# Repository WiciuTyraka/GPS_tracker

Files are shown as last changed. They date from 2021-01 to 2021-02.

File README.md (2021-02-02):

# Rocket Localization System

## About

[PUT Rocket Lab](https://tyraka.pl/) jest Kołem Naukowym z Politechniki Poznańskiej zajmującym się projektowaniem, budowaniem oraz testowaniem technologii
rakietowych. Flagowym projektem zespołu jest budowa rakiety sondażowej
Hexa 2 napędzanej hybrydowym silnikiem rakietowym. Jednym z większych problemów, z jakimi przychodzi zmagać się inżynierom budującym
rakiety, jest ich odzysk. Podczas testów rakieta zostaje wystrzelona w
przestrzeń. Wysokość oraz uzyskiwana prędkość obiektu jest oszacowana z
dużą dokładnością. Komplikacje pojawiają się przy estymowaniu miejsca
spadku rakiety, gdyż jest ono zależne w głównej mierze od powodzenia się
wszystkich procedur lądowania oraz w dużym stopniu od czynników meteorologicznych. Istotą odzysku jest zlokalizowanie rakiety w celu znalezienia
części, które są zdatne do ponownego użycia oraz tych, które już nie zadziałają, ale by zanieczyszczały środowisko. Większość zespołów decyduje
się na bardzo drogie komercyjne rozwiązania, które mimo wszystko nie są
wolne od ograniczeń. W tym repozytorium przedstawiony jest autorski projekt systemu lokalizacji rakiet stratosferycznych.

- [Rocket Localization System](#rocket-localization-system)
  - [About](#about)
  - [GPS Tracker](#gps-tracker)
    - [Hardware](#hardware)
      - [Sensors and Components](#sensors-and-components)
      - [Schema](#schema)
      - [Board](#board)
    - [Software](#software)
      - [Block Diagram](#block-diagram)
  - [Receiver](#receiver)
    - [Hardware](#hardware-1)
      - [Sensors and Components](#sensors-and-components-1)
      - [Schema](#schema-1)
      - [Board](#board-1)
    - [Software](#software-1)
      - [Block Diagram](#block-diagram-1)
  - [LoRa Library - RadioTyraka](#lora-library---radiotyraka)
  - [Mobile App](#mobile-app)
    - [Software](#software-1)
  - [App's](#app's)

## GPS Tracker

Pierwszą częścia systemu lokalizacji jest GPS Tracker. Urządzenie to umieszczone wewnątrz rakiety, przy pomocy fal radiowych rozsyła informację na temat swojego aktualnego połorzenia w przestrzeni.

### Hardware

Do komunikacji radiowej ziemia-powietrze posłużyła warstwa fizyczna systemu dalekiego zasięgu - LoRa, protokuł łączności został zaimplementowany według potrzeb naszego zespołu. LoRa używa techniki modulacji z widmem rozproszonym CSS (ang. chirp spread spectrum), która jest uznawana za pierwszą niskokosztową implementację tego rodzaju modulacji do zastosowań komercyjnych. Długość i szerokość geograficzna pozyskiwane są za pomooca systemu nawigacji satelitarnej. Wysokość obliczana jest na podstawie odczytu ciśnienia atmosferycznego mierzonego przez barometr. Z uwagi na stosunkowo niską przepustowość łącza radiowego wszystkie nadmiarowe dane zapisywane sa w trwałej pamięci flash.

Urządzenie jest także wyposażone w akumulator litowo-polimerowy i moduł umożliwiający jego ładowanie przez złącze mini-USB. Cztery diody led pełnią rolę prostego interfejsu, który informuje użytkownika o bierzących ustawieniach. Ustawienia te mogą być konfigurowane poprzez deydkowaną aplikację, która pozwala na ustawienie takich parametrów jak kanał radiowy, moc transmitowanego sygnału oraz data rate. Komunikacja z aplikacją odbywa się poprzez uniwersalny port asynchroniczny - UART. Urządzenie posiada 4 pinowe złącze któe przy pomocy konwertera UART-USB umożliwia podłączenie do komputera. Ostatnim ważnym elementem urządzenia jest włącznik zasilania o logice bistabilnej. Urządzenie zostaje uruchomione poprzez wyciągnięcie specjalnej zworki, tzw "Remove before fly".

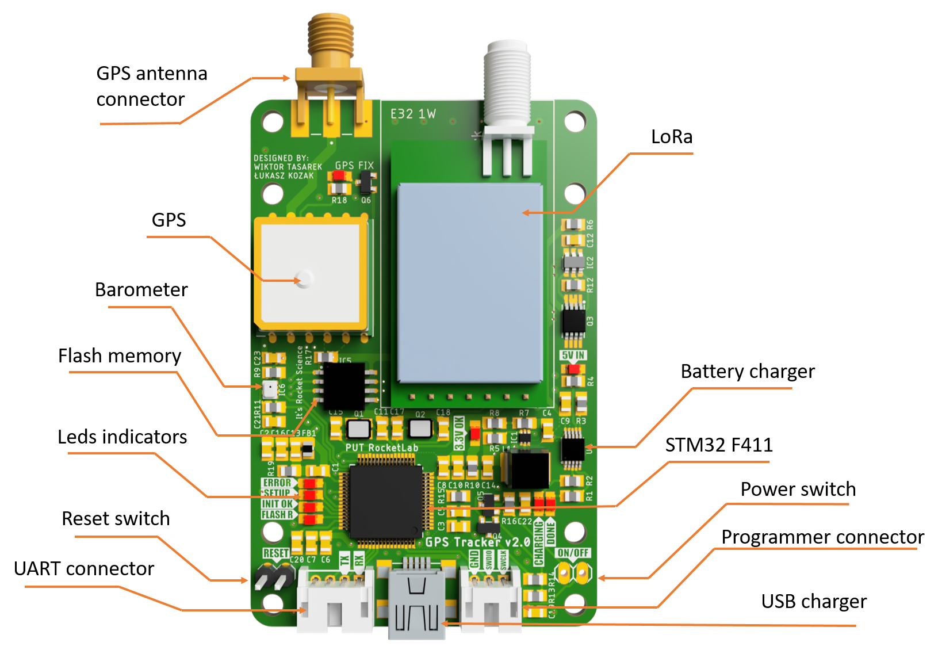
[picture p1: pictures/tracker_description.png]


<div align="center"><font size="2"><em>Figure 1. Render of GPS Tracker Board</em></font></div>

#### Sensors and components

<details>

Poniższa tabela przedstawia wszytkie moduły cyforwe wykorzystane w projekcie GPS tracker'a wraz z odnośnikiem do poszczególnych dokumentacji.

| Sensor | Device | Datasheet |
| --- | ---: | ---: |
| uC | STM32 F411 | [datasheet](Hardware/datasheet/stm32f411ce.pdf) |
| GPS | Quectel L80 | [datasheet](Hardware/datasheet/L80_Hardware_Design_V1.1.pdf) |
| Radio | LoRa E32-ttl-1W | [datasheet](Hardware/datasheet/E32-433T30D_Usermanual.pdf) |
| Barometer | BMP280 | [Hardware/datasheet](datasheet/BST-BMP280.pdf) |
| Flash memory | W25Q128 | [Hardware/datasheet](datasheet/w25q128fv.pdf) |
| Battery charger | MCP73833-AMI/UN | [Hardware/datasheet](datasheet/22005a-76648.pdf) |

</details>

#### Schema

<details>

Poniżej przedstawiony został dokładny schemat GPS tracker'a.

- [link do pliku z schematem](Hardware/gps_tracker2.0/gps_tracker2.0.sch)

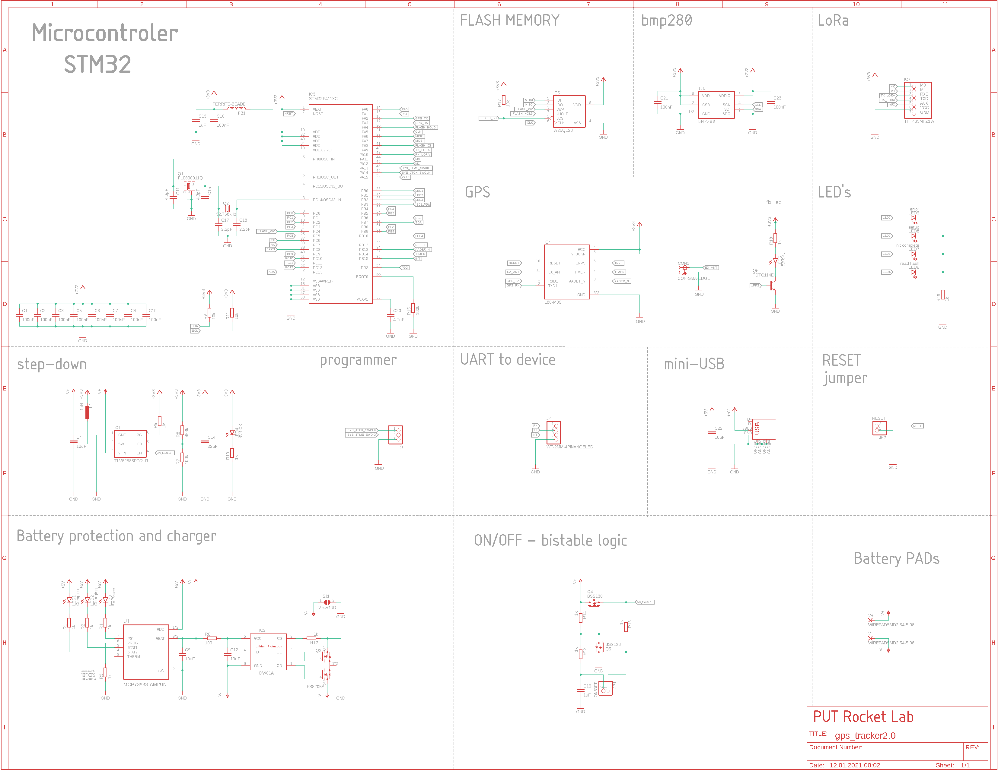
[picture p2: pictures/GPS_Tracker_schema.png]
schema


<div align="center"><font size="2"><em>Figure 2. Schema of GPS Tracker</em></font></div>

</details>

#### Board

<details>

Na poniższym obrazku przedstawione zostały obie strony dwustronnej płytki PCB, która łączy wszytskie elementy. Lewa strona (niebieskie ścieżki) przedstawia dolną warstwę natomiast prawa (czerwone ścieżki) górną warstwę.

- [link do piku z płytką PCB](Hardware/gps_tracker2.0/gps_tracker2.0.sch)

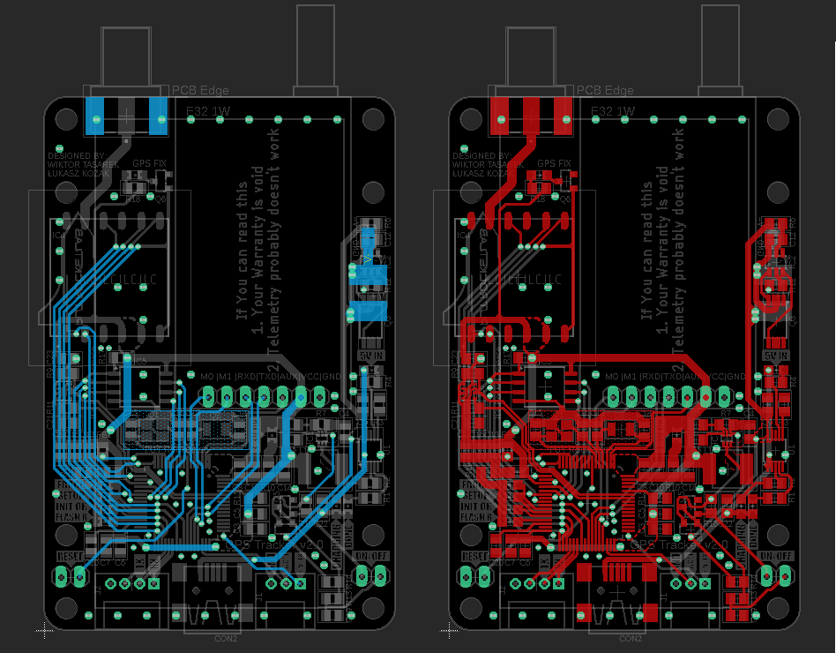
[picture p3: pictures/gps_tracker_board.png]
board


<div align="center"><font size="2"><em>Figure 3. GPS Tracker board</em></font></div>

</details>

### Software

Napisanie oprogramowania obsługującego moduły urządzenia oraz utworzenie protokołu komunikacyjnego jest niezbędne, by obsłużyć hardware i spełnić wymagania,
które stawiane są przed GPS Tracker'em. W tym celu wykorzystany został popularny framework STM32duino wraz, który jest wygodną i przyjemną platformą do tworzenia aplikacji dla
systemów wbudowanych.
GPS Tracker działa w oparciu o system czasu rzeczywistego FreeRTOS, aby dawać gwarancję wykonania zadań w określonym czasie. Symulacja wielowątkowego działania procesora pozwala
na odczytywanie danych z wszytskich sensorów z maksymalną częstotliwością czujników. Wszystkie dane zapisywane są w trwałej pamięci flash, dzięki czemu po znaleieniu rakiety mogą zostać one odczytane, a na ich podstawie możliwe jest wykreślenie na mapie dokładnego toru lotu rakiety.

Na potrzeby obsługi nowoczesnego modułu komunikacji dalekiego zasięgu -
LoRa - została napisana dedykowana biblioteka. Więcej informacji na jej temat można znaleźć [tutaj](#lora-library---radiotyraka)

#### Block Diagram

<details>

Na pozniższym obrazku przedstawiony został schemat blokowy procesów wykonywanych w ramach działania systemu czasu rzeczywistego zaimplementowanego na potrzeby obługi GPS Tracker'a.

- [link do pliku z kodem źródłowym GPS Tracker'a](Software/gps_tracker/transmiterRTOS_ConfigRadioTyraka.ino)

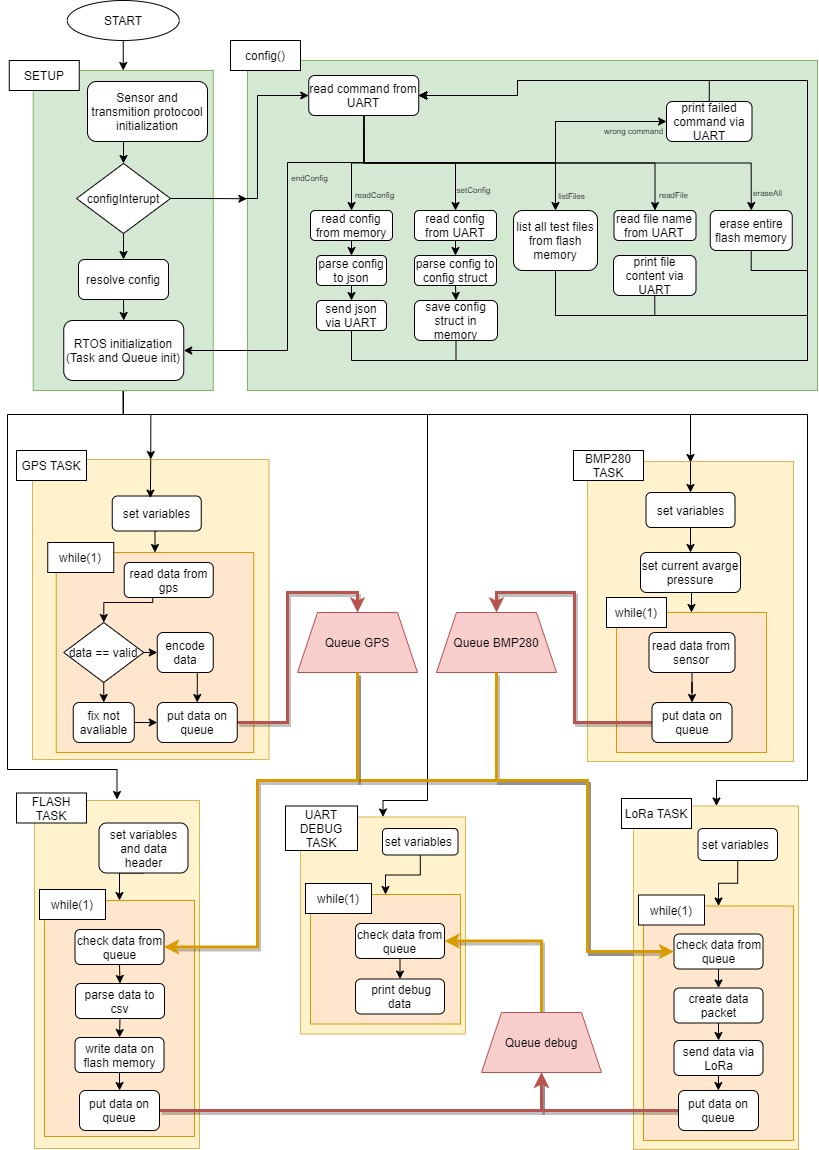
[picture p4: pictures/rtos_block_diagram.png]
block_diagrm


<div align="center"><font size="2"> <em>Figure 4. GPS Tracker code diagram</em></font></div>

</details>

## Receiver

Drugą częścią systemu jest Receiver, który wraz z smartfonem tworzy stację odbiorczą dla sygnału emitowanego z rakiety. Urządzenie wyposażone w antenę kierunkową pozwala na łączność z rakietami odbywającymi loty stratosferyczne. Odebrane dane wizualizowane są w czasie rzeczywistym na mapie satelitarnej na ekranie połączonego smartfona.

### Hardware

Receiver jest stosunkowo prostym urządzeniem, wyposażoy jest oczywiście w odbiornik radiowy umożliwiający nawiązenie komunikaji radiowej z rakietą oraz jego działanie oparte jest o mikrokontroler ESP32, który posiada zintegrowany moduł Bluetooth i Wi-Fi. Urządzenie wyposażone jest także w 4 złącza umożliwiające komunikację przewodową poprzez różne protokoły, takie jak 2x UART, SPI, I2C. Zastosowanie tak mnogiej liczby interfejsów sprawia, że receiver jest bardzo uniwersalnym urządzeniem, które może zostać w łatwy i przyjemny sposób wykorzystane w wielu projektach jako gateway dla sygnału radiowego LoRa.

Na potrzeby naszego systemu wykorzystywane są trzy interfejsy. Przy pomocy standardu bezprzewodowego Bluetooth Receiver łączy się z smartfonem który przy pomocy dedykowanej aplikacji staje wyświetlaczem dla danych telemetrycznych odbieranych z rakiety.
standard komunikacji Wi-Fi, wykorzystywany jest do postowania odebranych danych na server za pomocą rest api.
Użytkownik ma dostęp do nich poprzez naszą aplikację, która archiwizuje i umożliwia przeglądanie wszystkich danych z różnych lotów i testów.
Ostatnim wykorzystanym interfejsem jest UART, podpobnie jak w przypadku GPS Tracker'a służy on do konfigurowania parametrówtransmisji takich jak kanał radiowy, moc transmitowanego sygnału oraz data rate.

receiver_render

<div align="center"><font size="2"><em>Figure 1. Render of Receiver Board</em></font></div>

#### Sensors and components

<details>

Poniższa tabela przedstawia wszytkie moduły cyforwe wykorzystane w projekcie GPS tracker'a wraz z odnośnikiem do poszczególnych dokumentacji.

| Sensor | Device | Datasheet |
| --- | ---: | ---: |
| uC | ESP32 | [datasheet](Hardware/datasheet/esp32_datasheet.pdf) |
| Radio  | LoRa E32-ttl-1W | [datasheet](Hardware/datasheet/E32-433T30D_Usermanual.pdf) |

</details>

#### Schema

<details>

Poniżej przedstawiony został dokładny schemat Receivera.

- [link do pliku z schematem](Hardware/receiver/receiver.sch)

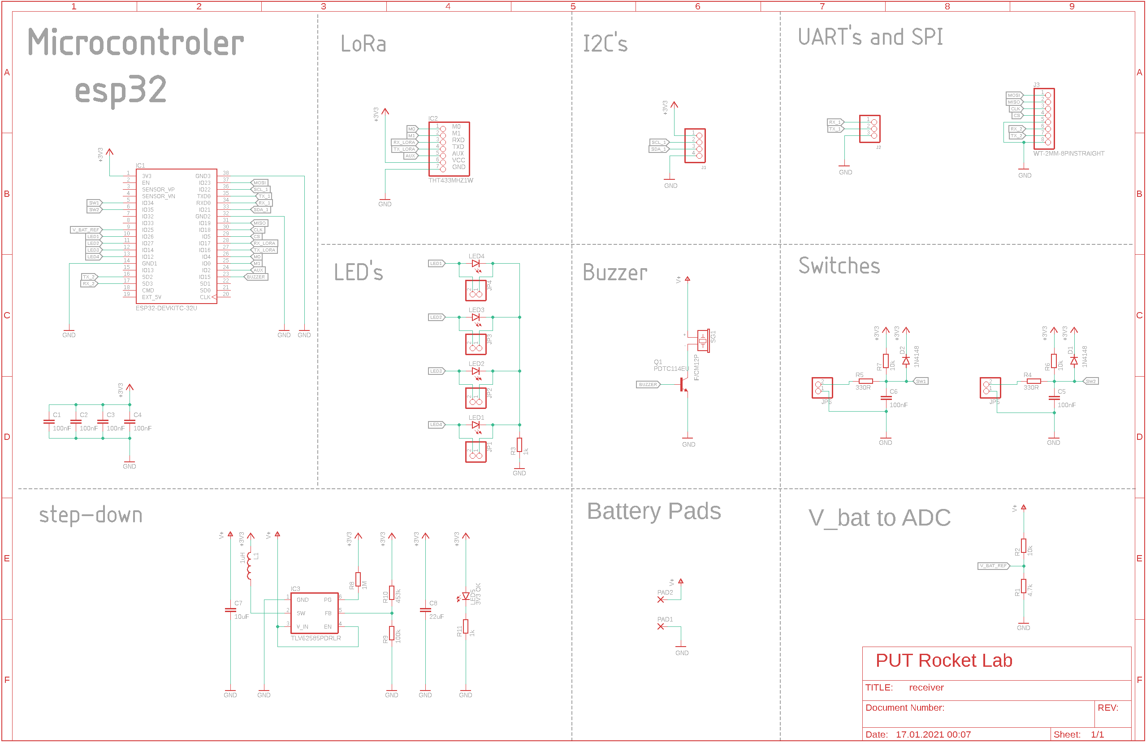
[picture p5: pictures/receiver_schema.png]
schema


<div align="center"><font size="2"><em>Figure 5. Schema of Receiver</em></font></div>

</details>

#### Board

<details>

Na poniższym obrazku przedstawione zostały obie strony dwustronnej płytki PCB, która łączy wszytskie elementy. Lewa strona (niebieskie ścieżki) przedstawia dolną warstwę natomiast prawa (czerwone ścieżki) górną warstwę.

- [link do piku z płytką PCB](Hardware/receiver/receiver.brd)

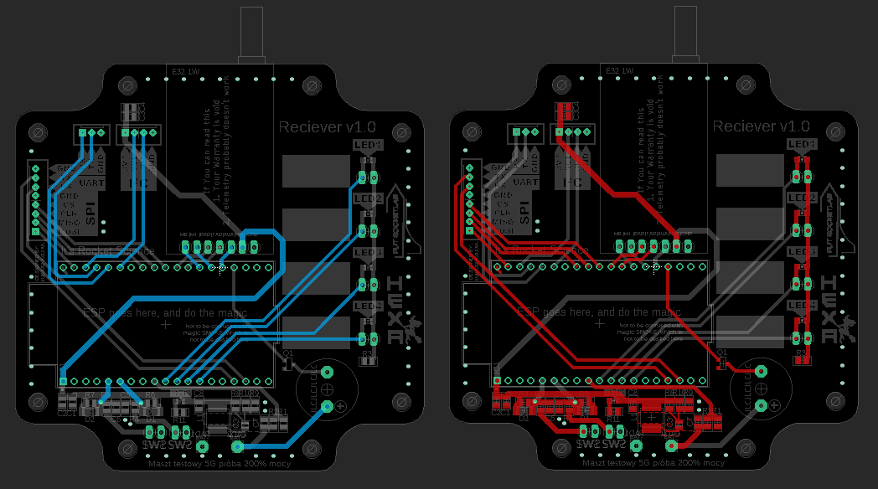
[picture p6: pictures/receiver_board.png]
board


<div align="center"><font size="2"><em>Figure 6. Receiver board</em></font></div>

</details>

### Software

Podobnie jak w przypadku GPS Tracker'a kod został napisany z wykorzystaniem freamworku Arduino. Jednak w tym przypadku system czasu rzeczywistego nie został wykorzystany, kod działa w sposób proceduralny.
Do obsługi modułu komunikacji radiowej, również została wykorzystana autorska biblioteka.

#### Block Diagram

<details>

Na pozniższym obrazku przedstawiony został schemat blokowy proceduralnego kodu Receiver'a

- [link do pliku z kodem źródłowym Receiver'a](Software/receiver/eciverRadioTyrakaV2.ino)

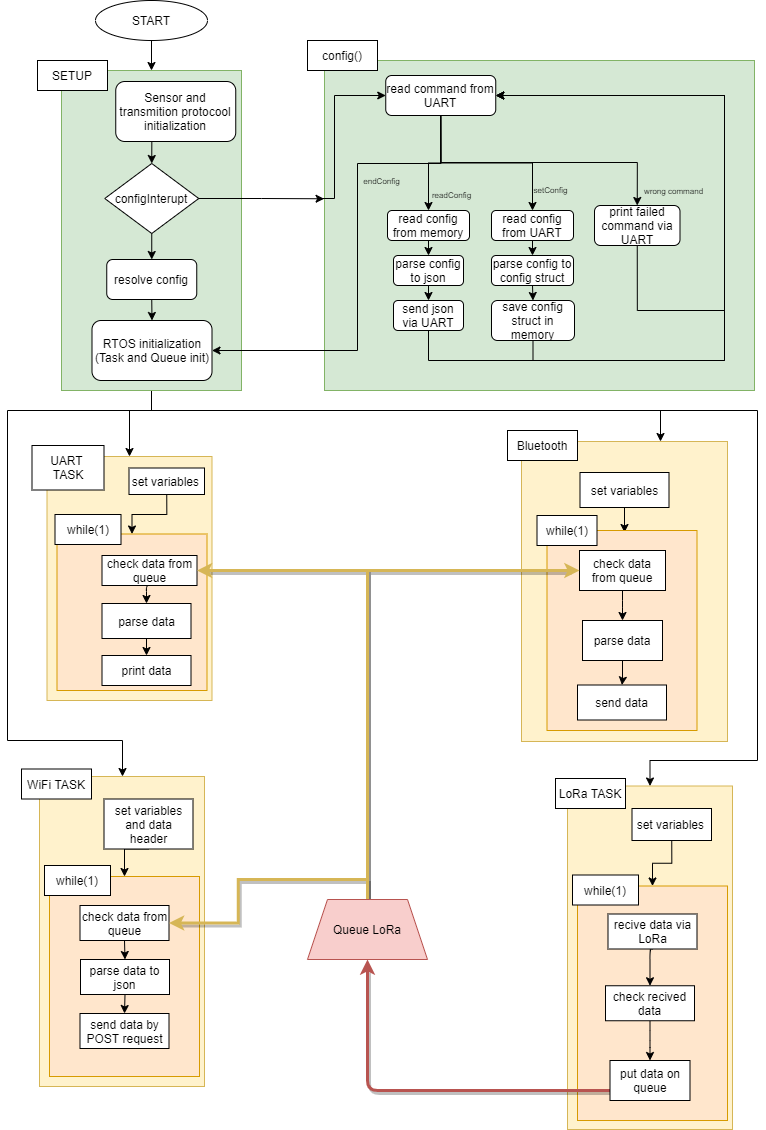
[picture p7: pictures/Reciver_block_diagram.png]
block_diagram


<div align="center"><font size="2"> <em>Figure 7. Receiver code diagram</em></font></div>

</details>

## LoRa Library - RadioTyraka

Na potrzeby obsługi nowoczesnego modułu komunikacji dalekiego zasięgu -
LoRa - została napisana dedykowana biblioteka. Biblioteka implementuje protokuł komunkacyjny, który znacząco ułatwia komunikację radiową natomiast obsługa modułu jest przyjamna dla użytkownika. Wydajność łącza radiowego uzyskana dzięki oprogramowaniu naszego zespołu jest większa niż w przypadku użytkowania biblioteki afirmowanej przez producenta modułu.

RadioTyraka powstało jako nakładka na popularną bibliotekę [RadioHead](https://www.airspayce.com/mikem/arduino/RadioHead/). Znacząco usprawnia ona niektóre z funkcji oferowanych przez bibliotekę, a także wprowadza nowe użyteczne rozwiązania. Biblioteka RadioTyraka znajduje się na osobnym repozytorium, które zawiera jej szczegółową dokumentację.

- [link do repozytorium z biblioteką](https://github.com/WiciuTyraka/RadioTyraka)

## Mobile App

W celu wizualizacji lokalizacji szukanego obiektu stworzona została aplikacja mobilna. Aplikacja łączy się za pomocą technologii Bluetooth ze
stacją odbiorczą i pobiera dane dotyczące aktualnej lokalizacji rakiety w czasie rzeczywistym. Dane wizualizowane są na mapie satelitarnej, co
znacznie przyspiesza i ułatwia proces odzyskiwania rakiety.

W celu poprawnego skonfigurowania Receivera ze smartphonem należy w ustawieniach bluetooth telefonu wyszukać i połączyć się z stacją odbiorczą.
Następnie w menu ustawień aplikacji (rys. 8) należy wybrać opcję **connect to paired device**.
W nowym oknie (rys. 9) z sparowanymi urządzeniami, należy wybrać odpowiednie urządzenie i wybrać **select**.
Dzięki temu przejdziemy do głównego okna (rys. 10) z widokiem mapy satelitarnej.

| | |
| :---: | :---: |
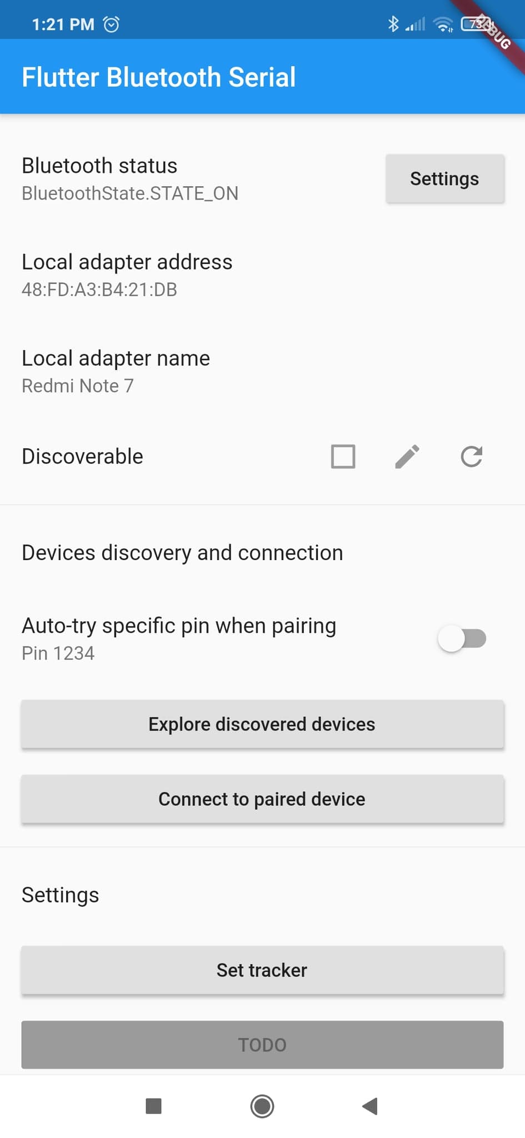
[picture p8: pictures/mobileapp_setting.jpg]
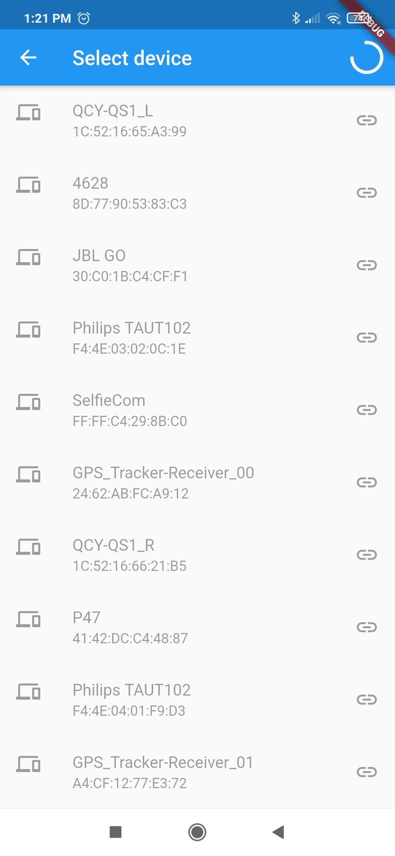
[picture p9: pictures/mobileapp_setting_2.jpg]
|  |  |

 <div align="center"><font size="2"><em>Figure 8. Mobile app setting </em></font> &nbsp;&nbsp;&nbsp;&nbsp;&nbsp;&nbsp;&nbsp;&nbsp;&nbsp;&nbsp;&nbsp;&nbsp;&nbsp;&nbsp;&nbsp;&nbsp;&nbsp;&nbsp;&nbsp;&nbsp;&nbsp;&nbsp;&nbsp;&nbsp;&nbsp;&nbsp;&nbsp;&nbsp;&nbsp;&nbsp;&nbsp;&nbsp;&nbsp;&nbsp;&nbsp;&nbsp; <font size="2"><em>Figure 9. Mobile app setting 2 </em></font></div>

&nbsp;

Czerwonym znacznikiem oznaczony jest lokalizowany obiket - lokalizacja trckera.
Po kliknięciu na znacznik użytkownik zostanie przeniesiony do map google na których zaznaczona będzie najkrótsza trasa od użytkownika do poszukiwanego obiektu.
w lewym górnym rogu wyświetlany jest czas od ostatniej otrzymanej wiadomośći.

&nbsp;

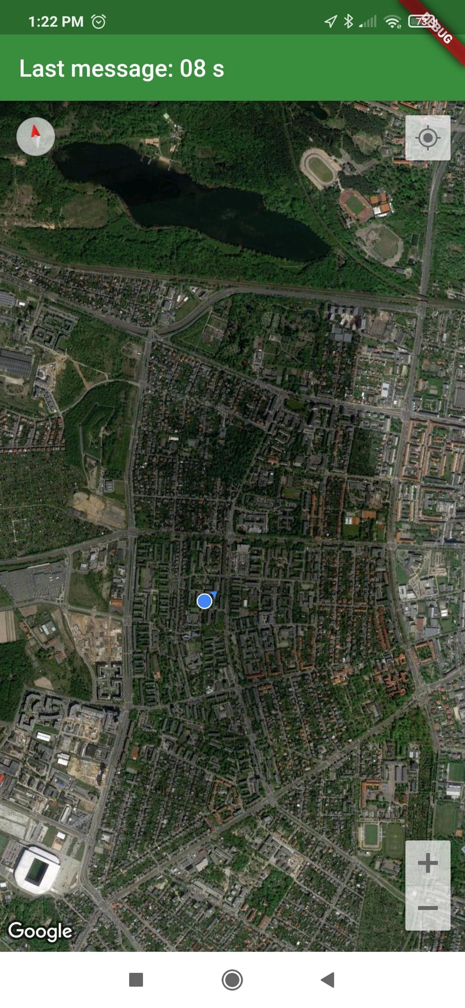
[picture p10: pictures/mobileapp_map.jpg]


<div align="center"><font size="2"><em>Figure 10.  Mobile app satelite map display </em></font></div>

## APP's

Niniejsza praca dyplomowa została zrealizowana wraz z awioniką Tyraka w ramach przedmiotu "Zespołowy projekt inżynierski" na Wydziale Informatyki i Matematyki Uniwersytetu im. Adama Mickiewicza w Poznaniu. Produkty projektu przeznaczone są dla koła rakietowego Politechniki Poznańskiej. Jest to aplikacja, która pozwala na uporządkowanie, analizę, przechowywanie i wyświetlanie danych z testów rakiet oraz silników. Dzięki temu mamy podgląd do danych z czujników na żywo podczas testów, dane są przedstawiane w postaci wykresów oraz mapy z lokalizacją rakiety co ułatwia odczyt danych. Trzeba zadbać o to, by dane były poprawnie zapisane, aby po teście móc wykonać analizę — w tym celu dane będą eksportowe do Excela. W przypadku testu silnika aplikacja oblicza średni ciąg, czas spalania, impuls całkowity oraz właściwy. Testy będą sortowane oraz filtrowane, aby ułatwić do nich dostęp. Aplikacja umożliwia konfigurowanie oraz kontrolowanie modułów elektronicznych, zmianę parametrów uruchomieniowych modułu, odczyt danych i czyszczenie pamięci flash.

Desktopowa aplikacja serwerowa odpowiada za odczytywanie danych wysyłanych przez elektronikę naziemną oraz przekazywanie ich w czasie rzeczywistym do aplikacji desktopowej. Zapisuje też ona otrzymane pomiary do odpowiednich plików JSON, w celu późniejszego wysłania ich do aplikacji webowej.

Serwer lokalny umożliwia również komunikację poprzez interfejs USB z komaptybilnym urządzeniem takim jak GPS tracker lub Receiver. Dzięki temu użytkownik jest w stanie wysyłać do niej polecenia i ma możliwość jej prostej konfiguracji, bez znajomości języka C++. Użytkownik ma też możliwość pobierania i czytania plików bezpośrednio z płytki urządzenia.

Głównym zadaniem webowej aplikacji serwerowej jest gromadzenie i możliwość eksportu danych historycznych do formatu JSON oraz CSV. Każdy użytkownik ma możliwość zalogowania się i dostęp do ograniczonych funkcjonalności aplikacji. Pełen dostęp posiada administrator, który zakłada konta użytkowników i zarządza aplikacją. Serwer webowy korzysta z nierelacyjnej bazy danych. Użytkownicy mają możliwość wyszukiwania konkretnych testów, jak i listowania większej ich ilości za pomocą dostępnych filtrów i funkcji sortujących.

Częścią projektu jest też strona internetowa, która ma pełnić funkcję wizytówki koła w Internecie. Na tej samej domenie co wizytówka będzie można zalogować się jako członek koła i uzyskać dostęp do panelu historii testów. Możliwa będzie analiza i odtworzenie zapisu live z przeprowadzonych testów. Oprócz ich wyświetlania będzie można wgrywać nowe testy z plików oraz eksportować je w formacie JSON i CSV. Kolejną częścią systemu Tyraka jest aplikacja desktopowa stworzona za pomocą frameworka Electron, na której zobaczyć będzie można testy w czasie rzeczywistym, wgrywać testy z plików oraz konfigurować elektronikę. Aplikacja webowa oraz desktopowa napisana jest za pomocą frameworka Vue.js.

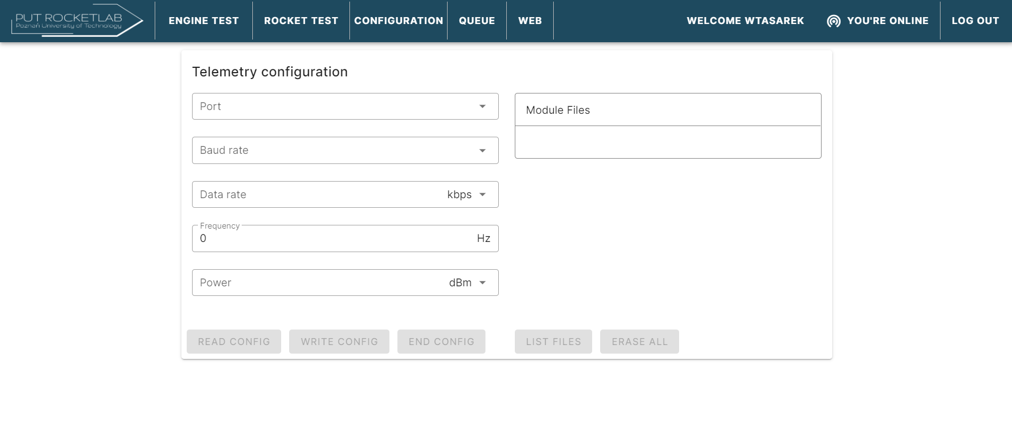
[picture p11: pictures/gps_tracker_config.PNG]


<div align="center"><font size="2"><em>Figure 11. config application for GPS tracker </em></font></div>

&nbsp;

&nbsp;

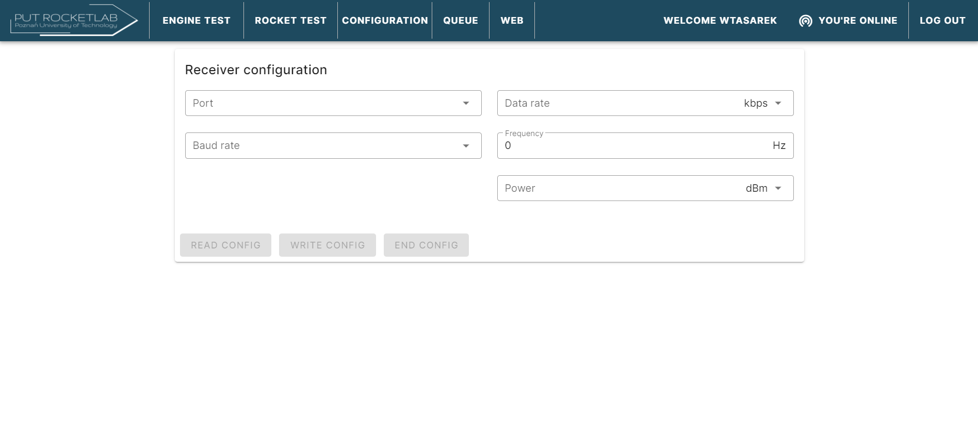
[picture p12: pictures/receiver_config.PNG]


<div align="center"><font size="2"><em>Figure 12. config application for Receiver </em></font></div>

&nbsp;

---

&nbsp;

_by Wiktor Tasarek_

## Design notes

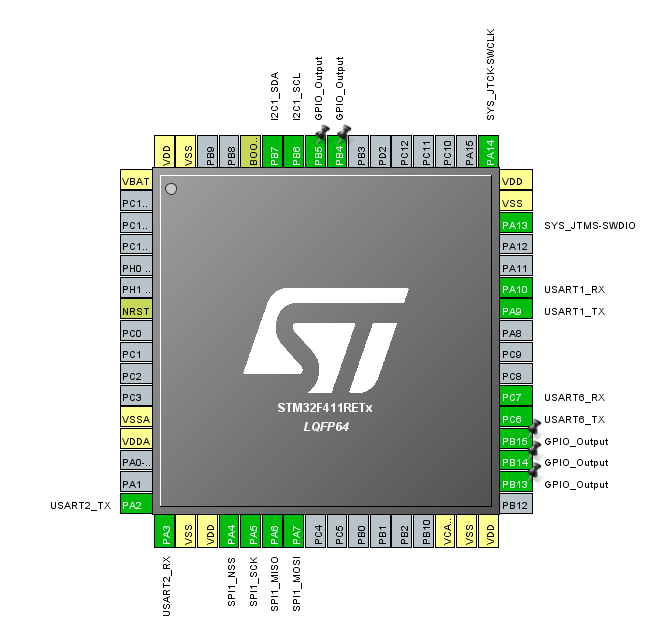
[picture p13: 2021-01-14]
Hardware/gps_tracker2.0/CubeMX.png

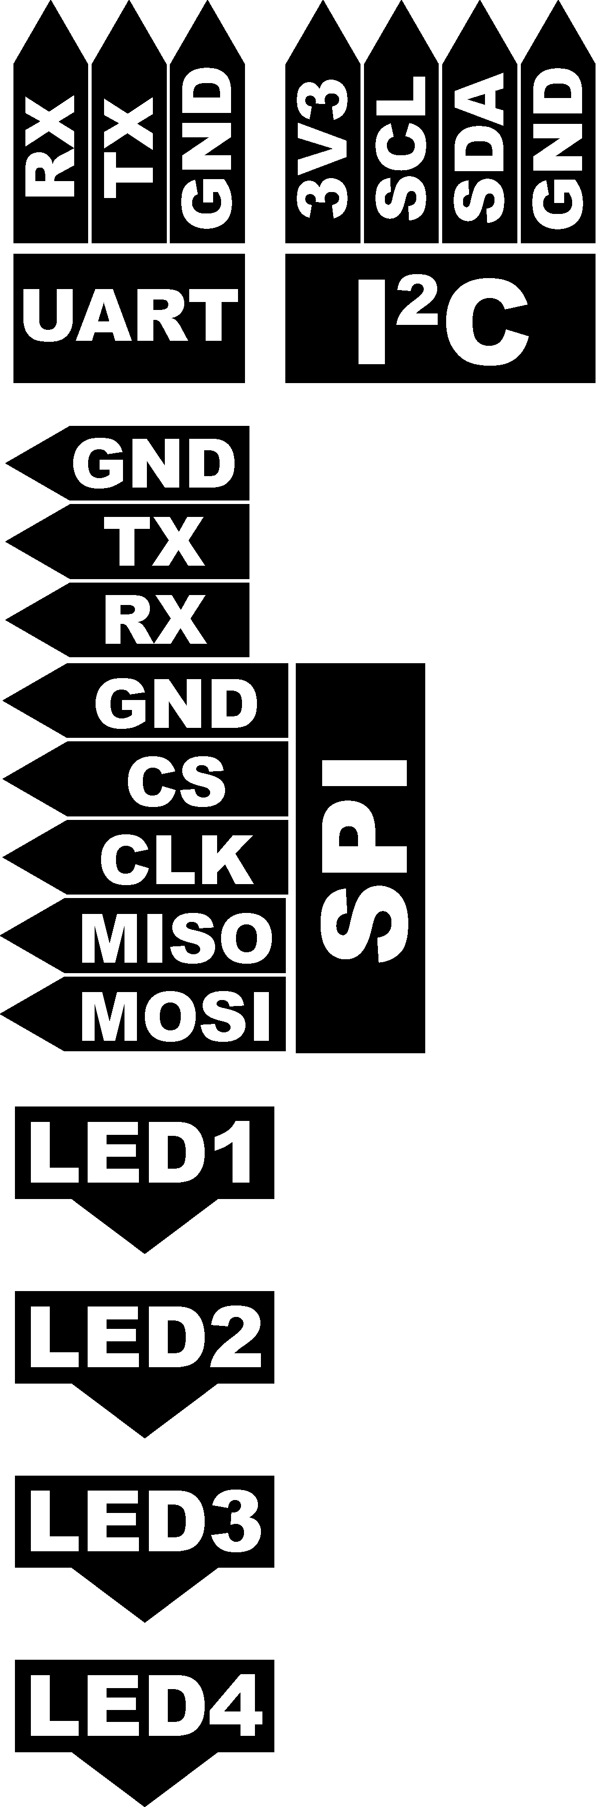
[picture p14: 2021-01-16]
Hardware/receiver/Legend.bmp

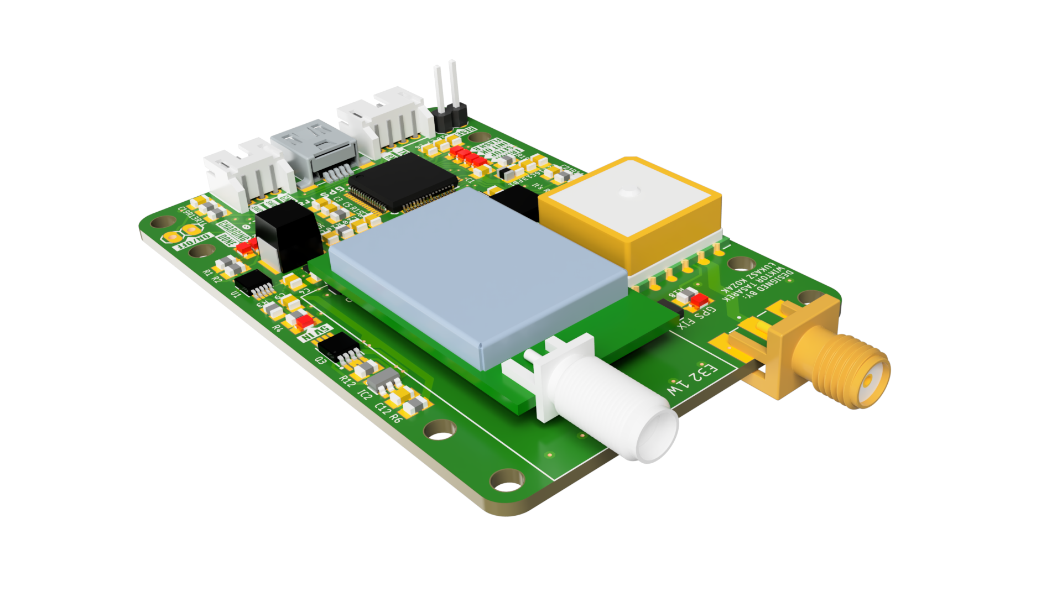
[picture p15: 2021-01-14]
pictures/tracker_izo_2.png

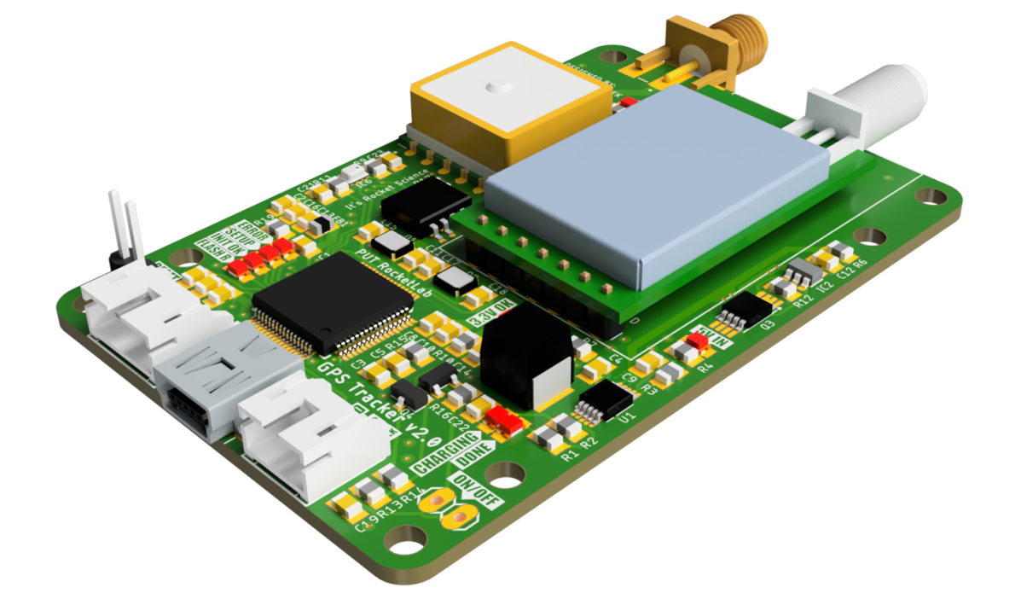
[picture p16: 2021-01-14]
pictures/tracker_izo.PNG

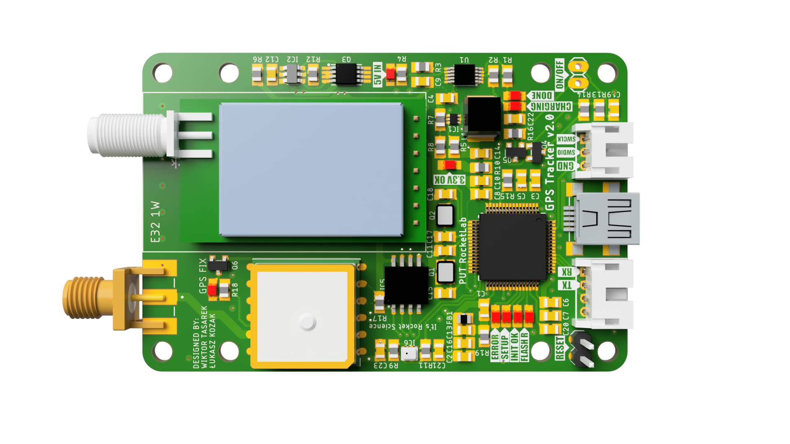
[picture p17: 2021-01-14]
pictures/tracker_top.png

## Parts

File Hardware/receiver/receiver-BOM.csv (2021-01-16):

Qty | Value | Device | Package | Parts | Comment | Description
6 | 100nF | C-EUC0805 | C0805 | C1, C2, C3, C4, C5, C6 |  | CAPACITOR, European symbol
1 | 10uF | C-EUC0805 | C0805 | C7 |  | CAPACITOR, European symbol
1 | 22uF | C-EUC0805 | C0805 | C8 |  | CAPACITOR, European symbol
2 | 1N4148 | DIODE-SOD80C | SOD80C | D1, D2 |  | DIODE
1 | ESP32-DEVKITC-32U | ESP32-DEVKITC-32U | MODULE_ESP32-DEVKITC-32U | IC1 |  | ESP32-DEVKITC Check prices
1 | THT433MHZ1W | THT433MHZ1W | E32M1000 | IC2
1 | TLV62585PDRLR | TLV62585PDRLR | SOT563 | IC3
1 | 1uH | L-USL5650M | L5650M | L1 |  | INDUCTOR, American symbol
4 |  | LEDCHIPLED_0805 | CHIPLED_0805 | LED1, LED2, LED3, LED4 | Blue | LED
1 | 3V3 OK | LEDCHIPLED_0805 | CHIPLED_0805 | LED5 | Red | LED
1 | PDTC114EU | BC846ASMD | SOT23 | Q1 |  | NPN Transistor
1 | 4.7k | R-EU_R0805 | R0805 | R1 |  | RESISTOR, European symbol
1 | 453k | R-EU_R0805 | R0805 | R10 |  | RESISTOR, European symbol
3 | 10k | R-EU_R0805 | R0805 | R2, R6, R7 |  | RESISTOR, European symbol
2 | 1k | R-EU_R0805 | R0805 | R3, R11 |  | RESISTOR, European symbol
2 | 330R | R-EU_R0805 | R0805 | R4, R5 |  | RESISTOR, European symbol
1 | 1M | R-EU_R0805 | R0805 | R8 |  | RESISTOR, European symbol
1 | 100k | R-EU_R0805 | R0805 | R9 |  | RESISTOR, European symbol
1 | F/CM12P | F/CM12P | F/CM12P | SG1 |  | BUZZER Source: Buerklin

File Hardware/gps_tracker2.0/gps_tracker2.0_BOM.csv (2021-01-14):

Qty | Value | Device | Package | Parts | Description | ARROW_ELECTRONICS-PURCHASE-URL | AVAILABILITY | DESCRIPTION | DIGIKEY-PURCHASE-URL | MF | MOUSER-PURCHASE-URL | MP | MPN | OC_FARNELL | OC_NEWARK | PACKAGE | POPULARITY | PRICE | SPICEPREFIX
1 | 100 | R-EU_R0805 | R0805 | R6 | RESISTOR, European symbol |  |  |  |  |  |  |  |  |  |  |  | 86 |  | R
2 | 100k | R-EU_R0805 | R0805 | R7, R15 | RESISTOR, European symbol |  |  |  |  |  |  |  |  |  |  |  | 86 |  | R
11 | 100nF | C-EUC0805 | C0805 | C1, C2, C3, C5, C6, C7, C8, C10, C16, C21, C23 | CAPACITOR, European symbol |  |  |  |  |  |  |  |  |  |  |  | 88 |  | C
3 | 10k | R-EU_R0805 | R0805 | R9, R11, R17 | RESISTOR, European symbol |  |  |  |  |  |  |  |  |  |  |  | 86 |  | R
4 | 10uF | C-EUC0805 | C0805 | C4, C9, C12, C22 | CAPACITOR, European symbol |  |  |  |  |  |  |  |  |  |  |  | 88 |  | C
1 | 1M | R-EU_R0805 | R0805 | R5 | RESISTOR, European symbol |  |  |  |  |  |  |  |  |  |  |  | 86 |  | R
11 | 1k | R-EU_R0805 | R0805 | R1, R2, R3, R4, R10, R12, R13, R14, R16, R18, R19 | RESISTOR, European symbol |  |  |  |  |  |  |  |  |  |  |  | 86 |  | R
2 | 1uF | C-EUC0805 | C0805 | C13, C19 | CAPACITOR, European symbol |  |  |  |  |  |  |  |  |  |  |  | 88 |  | C
1 | 1uH | L-EUL5650M | L5650M | L1 | INDUCTOR, European symbol |  |  |  |  |  |  |  |  |  |  |  | 0 |  | L
2 | 2.2pF | C-EUC0805 | C0805 | C17, C18 | CAPACITOR, European symbol |  |  |  |  |  |  |  |  |  |  |  | 88 |  | C
1 | 22uF | C-EUC0805 | C0805 | C14 | CAPACITOR, European symbol |  |  |  |  |  |  |  |  |  |  |  | 88 |  | C
1 | 32.768kHz | FC-135_32.768 | MC-405 | Q2 | kHz RANGE CRYSTAL UNIT SMD |  |  |  |  |  |  |  |  | unknown | unknown |  | 0
1 | 3V3 OK | LEDCHIPLED_0805 | CHIPLED_0805 | LED4 | LED |  |  |  |  |  |  |  |  |  |  |  | 52
2 | 4,3pF | C-EUC0805 | C0805 | C11, C15 | CAPACITOR, European symbol |  |  |  |  |  |  |  |  |  |  |  | 88 |  | C
1 | 4.7uF | C-EUC0805 | C0805 | C20 | CAPACITOR, European symbol |  |  |  |  |  |  |  |  |  |  |  | 88 |  | C
1 | 453k | R-EU_R0805 | R0805 | R8 | RESISTOR, European symbol |  |  |  |  |  |  |  |  |  |  |  | 86 |  | R
1 | 5V Power | LEDCHIPLED_0805 | CHIPLED_0805 | LED3 | LED |  |  |  |  |  |  |  |  |  |  |  | 52
1 | BMP280 | BMP280 | BMP280 | IC6 | The BMP280 is an absolute barometric pressure sensor especially designed for mobile applications. The sensor module is housed in an extremely compact 8-pin metal-lid LGA package with a footprint of only 2.0 × 2.5 mm2 and 0.95 mm package height. Its small
2 | BSS138 | BSS138 | SOT23 | Q4, Q5 | BSS138 N-Channel Logic Level Enhancement Mode Field Effect Transistor |  |  |  |  | Fairchild |  |  | BSS138 | 9845330 | 67R2009
1 | CON-SMA-EDGE | CON-SMA-EDGE | CINCH_142-0701-801 | CON1 | Conn SMA RCP 0Hz to 18GHz 50Ohm Solder ST Edge Mount Gold Check prices |  | Warning | SMA Connector Jack, Female Socket 50Ohm Board Edge, End Launch Solder | https://snapeda.com/shop?store=DigiKey&id=2691213 | Cinch Connectivity | https://snapeda.com/shop?store=Mouser&id=2691213 | 142-0701-801 |  |  |  | None |  | None
1 | Charging | LEDCHIPLED_0805 | CHIPLED_0805 | LED2 | LED |  |  |  |  |  |  |  |  |  |  |  | 52
1 | Complete | LEDCHIPLED_0805 | CHIPLED_0805 | LED1 | LED |  |  |  |  |  |  |  |  |  |  |  | 52
1 | DW01A | DW01A | SOT23-6 | IC2 |  |  | Unavailable | One Cell Lithium-ion/Polymer Battery Protection IC |  | Fortune Semiconductor |  | DW01A |  |  |  | SOT-23-6 Fortune Semiconductor |  | None
1 | FERRITE-BEADB | FERRITE-BEADB | 0805 | FB1 | Ferrite beads in various packages
1 | FL0800011Q | FL0800011Q | FL0800011Q | Q1 | kHz RANGE CRYSTAL UNIT SMD
1 | FS8205A | FS8205A | SOP65P640X120-8N | Q3 | N/A |  | Unavailable |  |  | Fortune Semiconductor |  | FS8205A |  |  |  | Package |  | None
1 | GPS fix | LEDCHIPLED_0805 | CHIPLED_0805 | LED5 | LED |  |  |  |  |  |  |  |  |  |  |  | 52
1 | L80-M39 | L80-M39 | XCVR_L80-M39 | IC4 | Check prices |  | Bad | L80 is an ultra compact GPS POT (Patch on Top) module with an embedded 15.0mm × 15.0mm × 4.0mm patch antenna. |  | Quectel |  | L80-M39 |  |  |  | None |  | None
1 | MCP73833-AMI/UN | MCP73833-AMI/UN | SOP50P490X110-10N | U1 | Check prices | https://snapeda.com/shop?store=Arrow+Electronics&id=142622 | Good | Charger IC Lithium Ion/Polymer 10-MSOP | https://snapeda.com/shop?store=DigiKey&id=142622 | Microchip | https://snapeda.com/shop?store=Mouser&id=142622 | MCP73833-AMI/UN |  |  |  | MSOP-10 Microchip |  | None
1 | ON/OFF | PINHD-1X2 | 1X02 | JP1 | PIN HEADER |  |  |  |  |  |  |  |  |  |  |  | 98
1 | PDTC114EU | BC846ASMD | SOT23 | Q6 | NPN Transistor |  |  |  |  |  |  |  |  |  |  |  | 0
1 | RESET | PINHD-1X2 | 1X02 | JP2 | PIN HEADER |  |  |  |  |  |  |  |  |  |  |  | 98
1 | STM32F411XC | STM32F411XC | LQFP64 | IC3
1 | THT433MHZ1W | THT433MHZ1W | E32M1000 | IC7
1 | TLV62585PDRLR | TLV62585PDRLR | SOT563 | IC1
1 | USB-SHIELD | USB-SHIELD | USB-M-S1 | CON2
1 | V-<>GND | SJ | SJ | SJ1 | SMD solder JUMPER |  |  |  |  |  |  |  |  |  |  |  | 33
1 | W25Q128 | W25Q128 | SO08-FLASH | IC5
2 | WIREPADSMD2,54-5,08 | WIREPADSMD2,54-5,08 | SMD2,54-5,08 | V+, V- | Wire PAD connect wire on PCB |  |  |  |  |  |  |  |  |  |  |  | 2
1 | WT-2MM-3PINANGELED | WT-2MM-3PINANGELED | W_TYPE_2MM_3_A | J1
1 | WT-2MM-4PINANGELED | WT-2MM-4PINANGELED | W_TYPE_2MM_4_A | J2
1 | error | LEDCHIPLED_0805 | CHIPLED_0805 | LED9 | LED |  |  |  |  |  |  |  |  |  |  |  | 52
1 | init complete | LEDCHIPLED_0805 | CHIPLED_0805 | LED7 | LED |  |  |  |  |  |  |  |  |  |  |  | 52
1 | read flash | LEDCHIPLED_0805 | CHIPLED_0805 | LED6 | LED |  |  |  |  |  |  |  |  |  |  |  | 52
1 | setup | LEDCHIPLED_0805 | CHIPLED_0805 | LED8 | LED |  |  |  |  |  |  |  |  |  |  |  | 52

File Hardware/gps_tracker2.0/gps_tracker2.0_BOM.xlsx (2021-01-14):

Qty | Value | Device | Package | Parts | Comment | Source
11 | 100nF | C-EUC0805 | C0805 | C1, C2, C3, C5, C6, C7, C8, C10, C16, C21, C23
2 | 4,3pF | C-EUC0805 | C0805 | C11, C15
2 | 1uF | C-EUC0805 | C0805 | C13, C19
1 | 22uF | C-EUC0805 | C0805 | C14
2 | 2.2pF | C-EUC0805 | C0805 | C17, C18
1 | 4.7uF | C-EUC0805 | C0805 | C20
4 | 10uF | C-EUC0805 | C0805 | C4, C9, C12, C22
1 | CON-SMA-EDGE | CON-SMA-EDGE | CINCH_142-0701-801 | CON1 | Złącze anteny GPS | https://pl.mouser.com/ProductDetail/Taoglas/EMPCBSMAFSTJBHT?qs=AL7xPqYNrmTeWSPxKT6oAw%3D%3D
1 | USB-SHIELD | USB-SHIELD | USB-M-S1 | CON2
1 | FERRITE-BEADB | FERRITE-BEADB | 0805 | FB1
1 | TLV62585PDRLR | TLV62585PDRLR | SOT563 | IC1
1 | DW01A | DW01A | SOT23-6 | IC2 | Wylut | https://abc-rc.pl/product-pol-9157-Modul-BMS-PCM-PCB-ladowania-i-ochrony-ogniw-Li-ion-1S-3-7V-3A-do-ogniw-18650.html
1 | STM32F411XC | STM32F411XC | LQFP64 | IC3 |  | ?
1 | L80-M39 | L80-M39 | XCVR_L80-M39 | IC4 |  | ?
1 | W25Q128 | W25Q128 | SO08-FLASH | IC5 |  | ?
1 | BMP280 | BMP280 | BMP280 | IC6 |  | ?
1 | THT433MHZ1W | THT433MHZ1W | E32M1000 | IC7 | LoRa
1 | 1uH | L-EUL5650M | L5650M | L1 | tak
1 | Complete | LEDCHIPLED_0805 | CHIPLED_0805 | LED1 | Green
1 | Charging | LEDCHIPLED_0805 | CHIPLED_0805 | LED2 | Yellow
1 | 5V Power | LEDCHIPLED_0805 | CHIPLED_0805 | LED3 | Red
1 | 3V3 OK | LEDCHIPLED_0805 | CHIPLED_0805 | LED4 | Red
1 | GPS fix | LEDCHIPLED_0805 | CHIPLED_0805 | LED5 | Blue
1 | read flash | LEDCHIPLED_0805 | CHIPLED_0805 | LED6 | Blue
1 | init complete | LEDCHIPLED_0805 | CHIPLED_0805 | LED7 | Blue
1 | setup | LEDCHIPLED_0805 | CHIPLED_0805 | LED8 | Blue
1 | error | LEDCHIPLED_0805 | CHIPLED_0805 | LED9 | Red
1 | FL0800011Q | FL0800011Q | FL0800011Q | Q1 | Kwarc
1 | 32.768kHz | FC-135_32.768 | MC-405 | Q2 | Kwarc
1 | FS8205A | FS8205A | SOP65P640X120-8N | Q3 | Wylut | https://abc-rc.pl/product-pol-9157-Modul-BMS-PCM-PCB-ladowania-i-ochrony-ogniw-Li-ion-1S-3-7V-3A-do-ogniw-18650.html
2 | BSS138 | BSS138 | SOT23 | Q4, Q5 | Przerzutnik 2 stan
1 | PDTC114EU | BC846ASMD | SOT23 | Q6
11 | 1k | R-EU_R0805 | R0805 | R1, R2, R3, R4, R10, R12, R13, R14, R16, R18, R19
1 | 1M | R-EU_R0805 | R0805 | R5
1 | 100 | R-EU_R0805 | R0805 | R6
2 | 100k | R-EU_R0805 | R0805 | R7, R15
1 | 453k | R-EU_R0805 | R0805 | R8
3 | 10k | R-EU_R0805 | R0805 | R9, R11, R17
1 | MCP73833-AMI/UN | MCP73833-AMI/UN | SOP50P490X110-10N | U1 | Ładowarka baterii | https://pl.mouser.com/ProductDetail/Microchip-Technology/MCP73833T-AMI-UN?qs=Fxu3fLyJv8cZVyNfuXhl2Q%3D%3D

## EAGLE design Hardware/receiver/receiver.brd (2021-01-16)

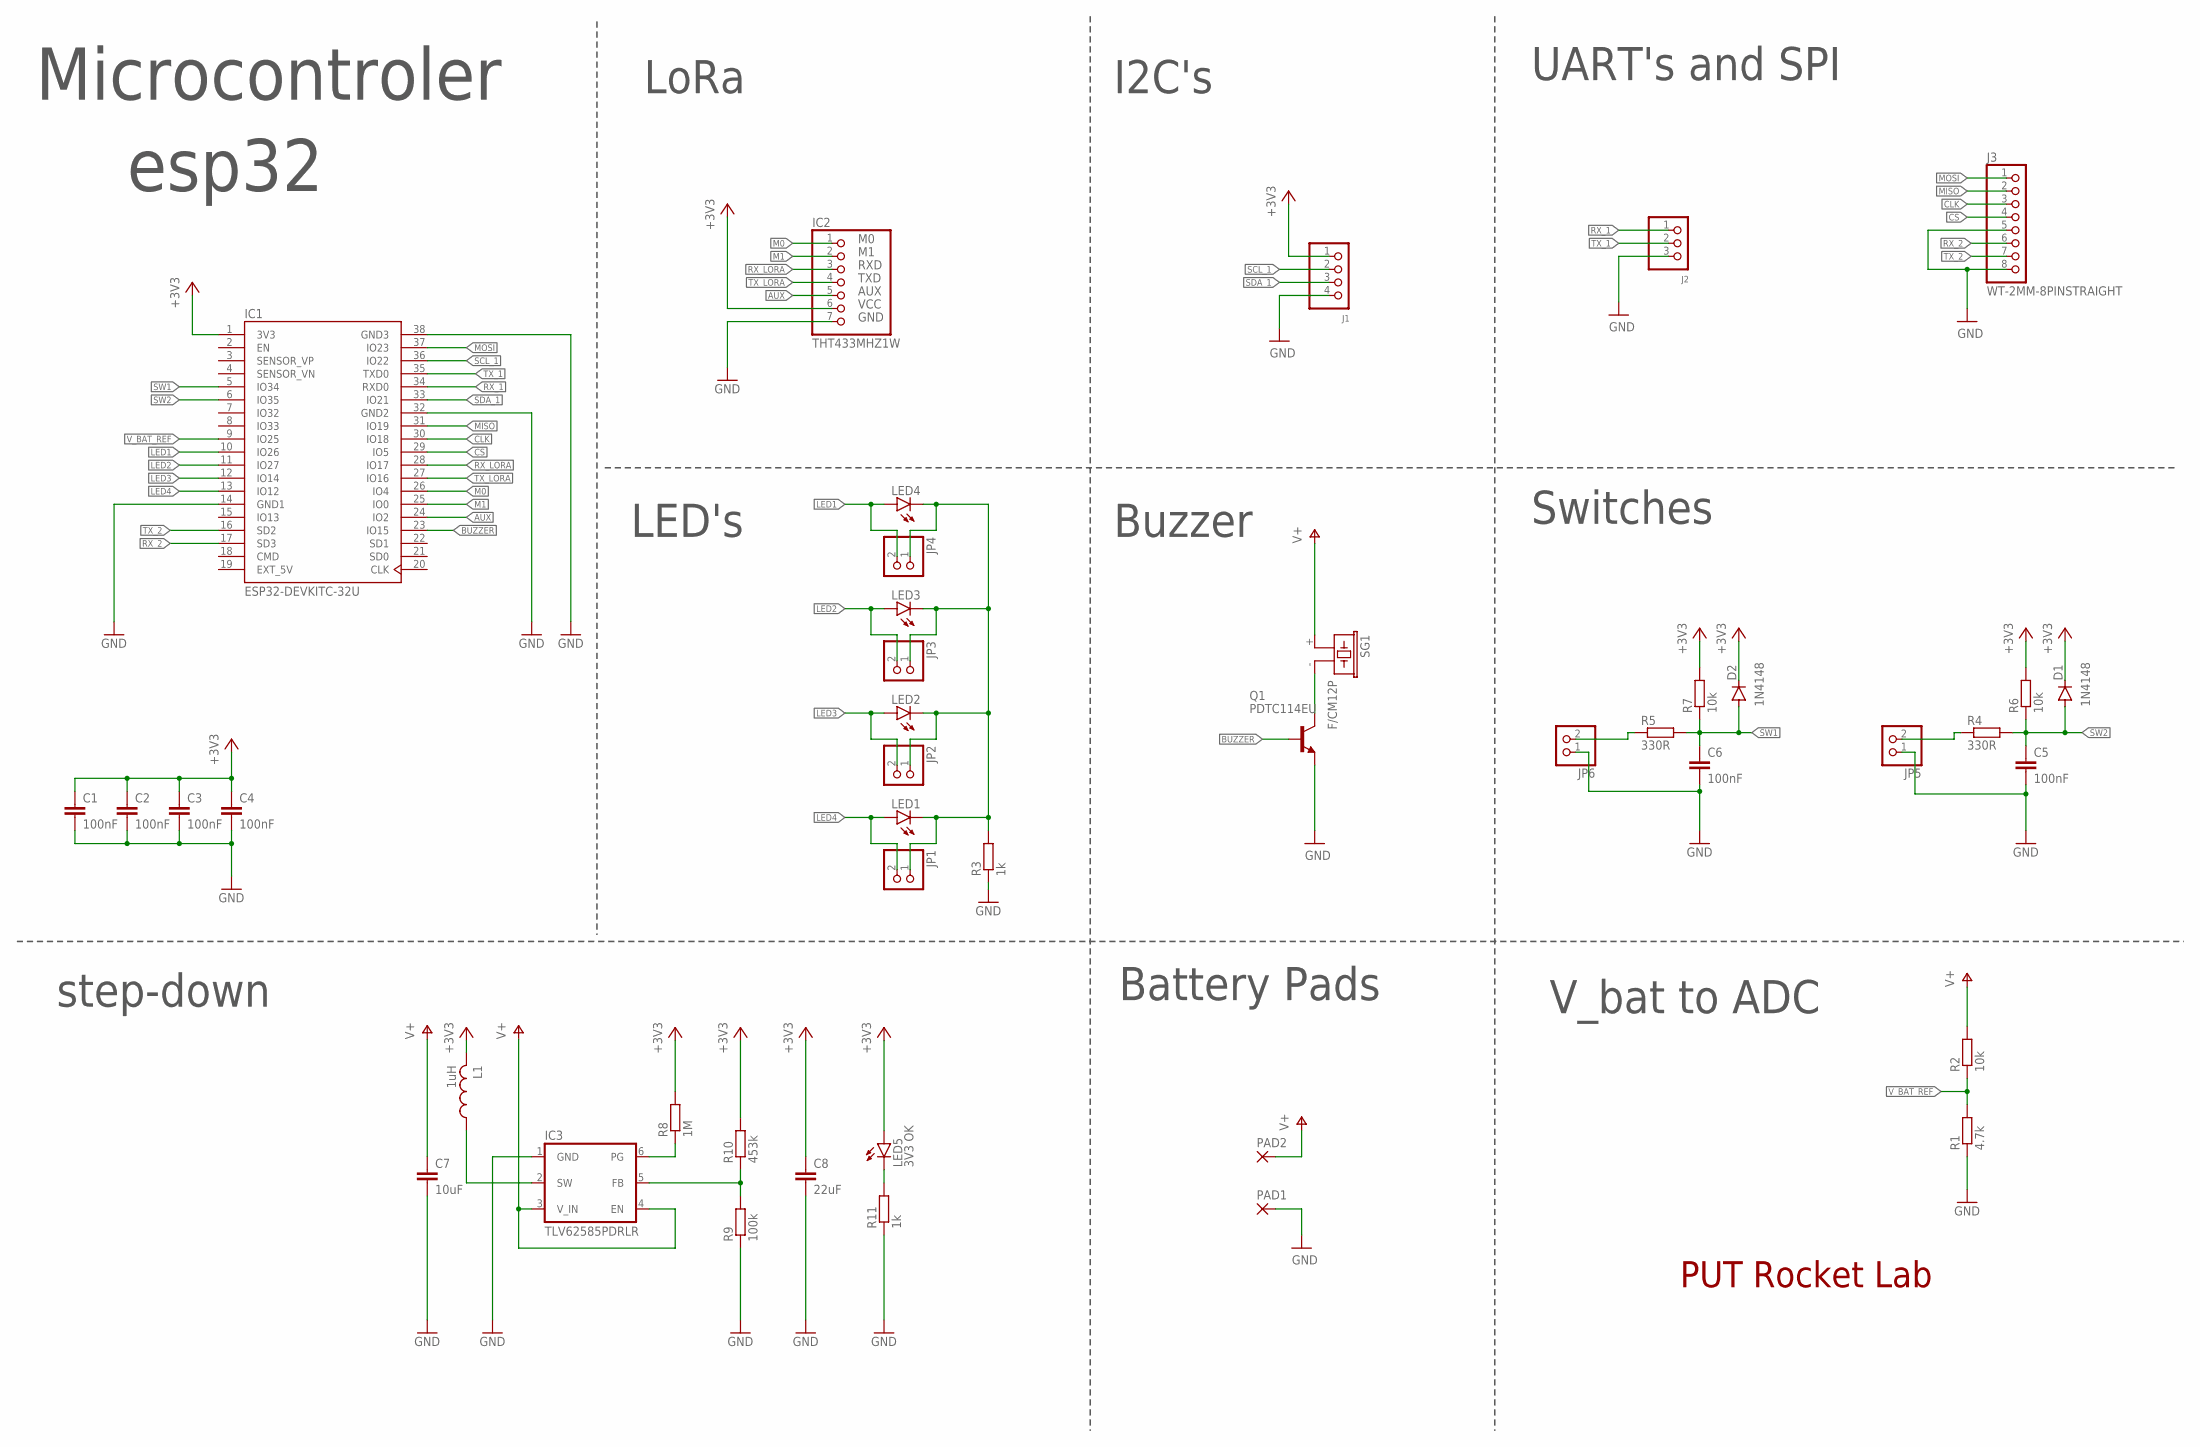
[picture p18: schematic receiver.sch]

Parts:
C1, C2, C3, C4, C5, C6: 100nF; C0805
C7: 10uF; C0805
C8: 22uF; C0805
D1, D2: 1N4148; SOD80C
IC1: ESP32-DEVKITC-32U; MODULE_ESP32-DEVKITC-32U
IC2: THT433MHZ1W; E32M1000
IC3: TLV62585PDRLR; SOT563
J1: WT-2MM-4PINSTRAIGHT; W_TYPE_2MM_4_N
J2: WT-2MM-3PINSTRAIGHT; W_TYPE_2MM_3_N
J3: WT-2MM-8PINSTRAIGHT; W_TYPE_2MM_8_N
JP1, JP2, JP3, JP4, JP5, JP6: PINHD-1X2; 1X02
L1: 1uH; L5650M
LED1, LED2, LED3, LED4: LEDCHIPLED_0805; CHIPLED_0805
LED5: 3V3 OK; CHIPLED_0805
PAD1, PAD2: WIREPAD2,54/1,1; 2,54/1,1
Q1: PDTC114EU; SOT23
R1: 4.7k; R0805
R2, R6, R7: 10k; R0805
R3, R11: 1k; R0805
R4, R5: 330R; R0805
R8: 1M; R0805
R9: 100k; R0805
R10: 453k; R0805
SG1: F/CM12P

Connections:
+3V3: C1.1, C2.1, C3.1, C4.1, C8.1, D1.C, D2.C, IC1.1 (3V3), IC2.6 (VCC), J1.1, L1.2, LED5.A, R6.2, R7.2, R8.2, R10.2
AUX: IC1.24 (IO2), IC2.5 (AUX)
BUZZER: IC1.23 (IO15), Q1.1 (B)
CLK: IC1.30 (IO18), J3.3
CS: IC1.29 (IO5), J3.4
EXT_5V: IC1.19 (EXT_5V)
GND: C1.2, C2.2, C3.2, C4.2, C5.2, C6.2, C7.2, C8.2, IC1.14 (GND1), IC1.32 (GND2), IC1.38 (GND3), IC2.7 (GND), IC3.1 (GND), J1.4, J2.3, J3.5, J3.8, JP5.1, JP6.1, PAD1.1, Q1.2 (E), R1.1, R3.1, R9.1, R11.1
LED1: IC1.10 (IO26), JP4.2, LED4.A
LED2: IC1.11 (IO27), JP3.2, LED3.A
LED3: IC1.12 (IO14), JP2.2, LED2.A
LED4: IC1.13 (IO12), JP1.2, LED1.A
M0: IC1.26 (IO4), IC2.1 (M0)
M1: IC1.25 (IO0), IC2.2 (M1)
MISO: IC1.31 (IO19), J3.2
MOSI: IC1.37 (IO23), J3.1
unnamed: JP1.1, JP2.1, JP3.1, JP4.1, LED1.C, LED2.C, LED3.C, LED4.C, R3.2
unnamed: LED5.C, R11.2
unnamed: IC3.5 (FB), R9.2, R10.1
unnamed: IC3.6 (PG), R8.1
unnamed: IC3.2 (SW), L1.1
unnamed: Q1.3 (C), SG1.- (2)
unnamed: JP6.2, R5.1
unnamed: JP5.2, R4.1
RX_1: IC1.34 (RXD0), J2.1
RX_2: IC1.17 (SD3), J3.6
RX_LORA: IC1.28 (IO17), IC2.3 (RXD)
SCL_1: IC1.36 (IO22), J1.2
SDA_1: IC1.33 (IO21), J1.3
SW1: C6.1, D2.A, IC1.5 (IO34), R5.2, R7.1
SW2: C5.1, D1.A, IC1.6 (IO35), R4.2, R6.1
TX_1: IC1.35 (TXD0), J2.2
TX_2: IC1.16 (SD2), J3.7
TX_LORA: IC1.27 (IO16), IC2.4 (TXD)
V+: C7.1, IC3.3 (V_IN), IC3.4 (EN), PAD2.1, R2.2, SG1.+ (1)
V_BAT_REF: IC1.9 (IO25), R1.2, R2.1

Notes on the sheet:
Microcontroler
esp32
LoRa
step-down
LED's
I2C's
UART's and SPI
Buzzer
Battery Pads
V_bat to ADC
Switches
PUT Rocket Lab

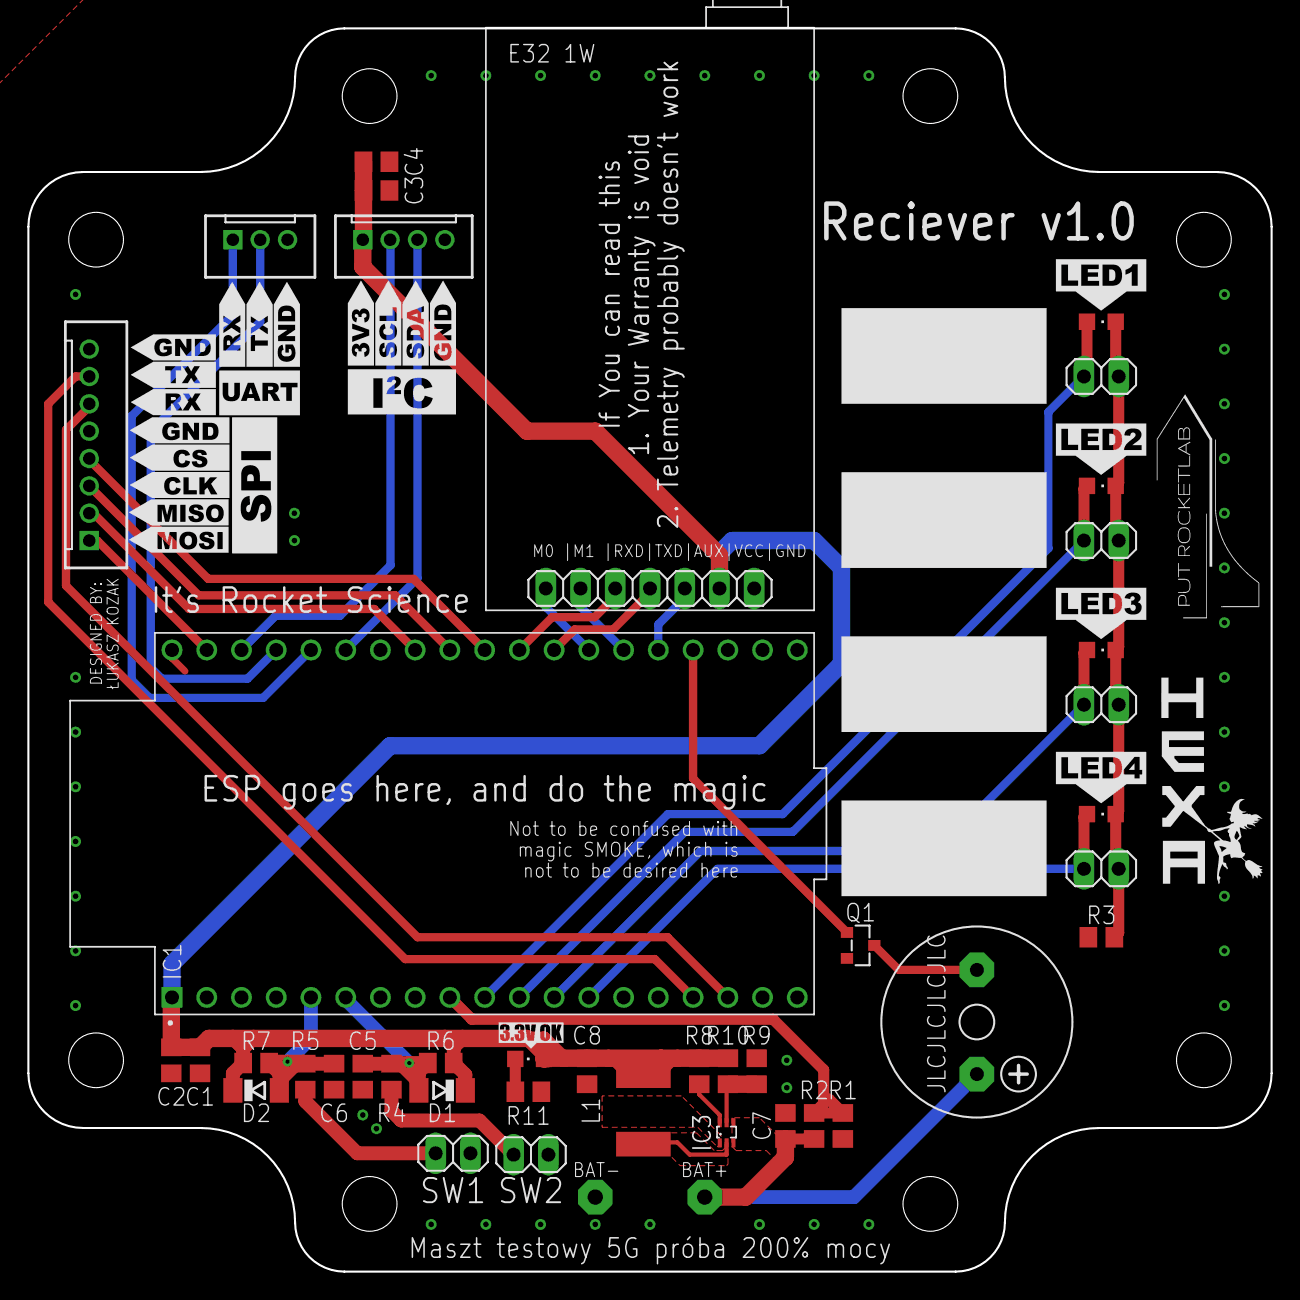
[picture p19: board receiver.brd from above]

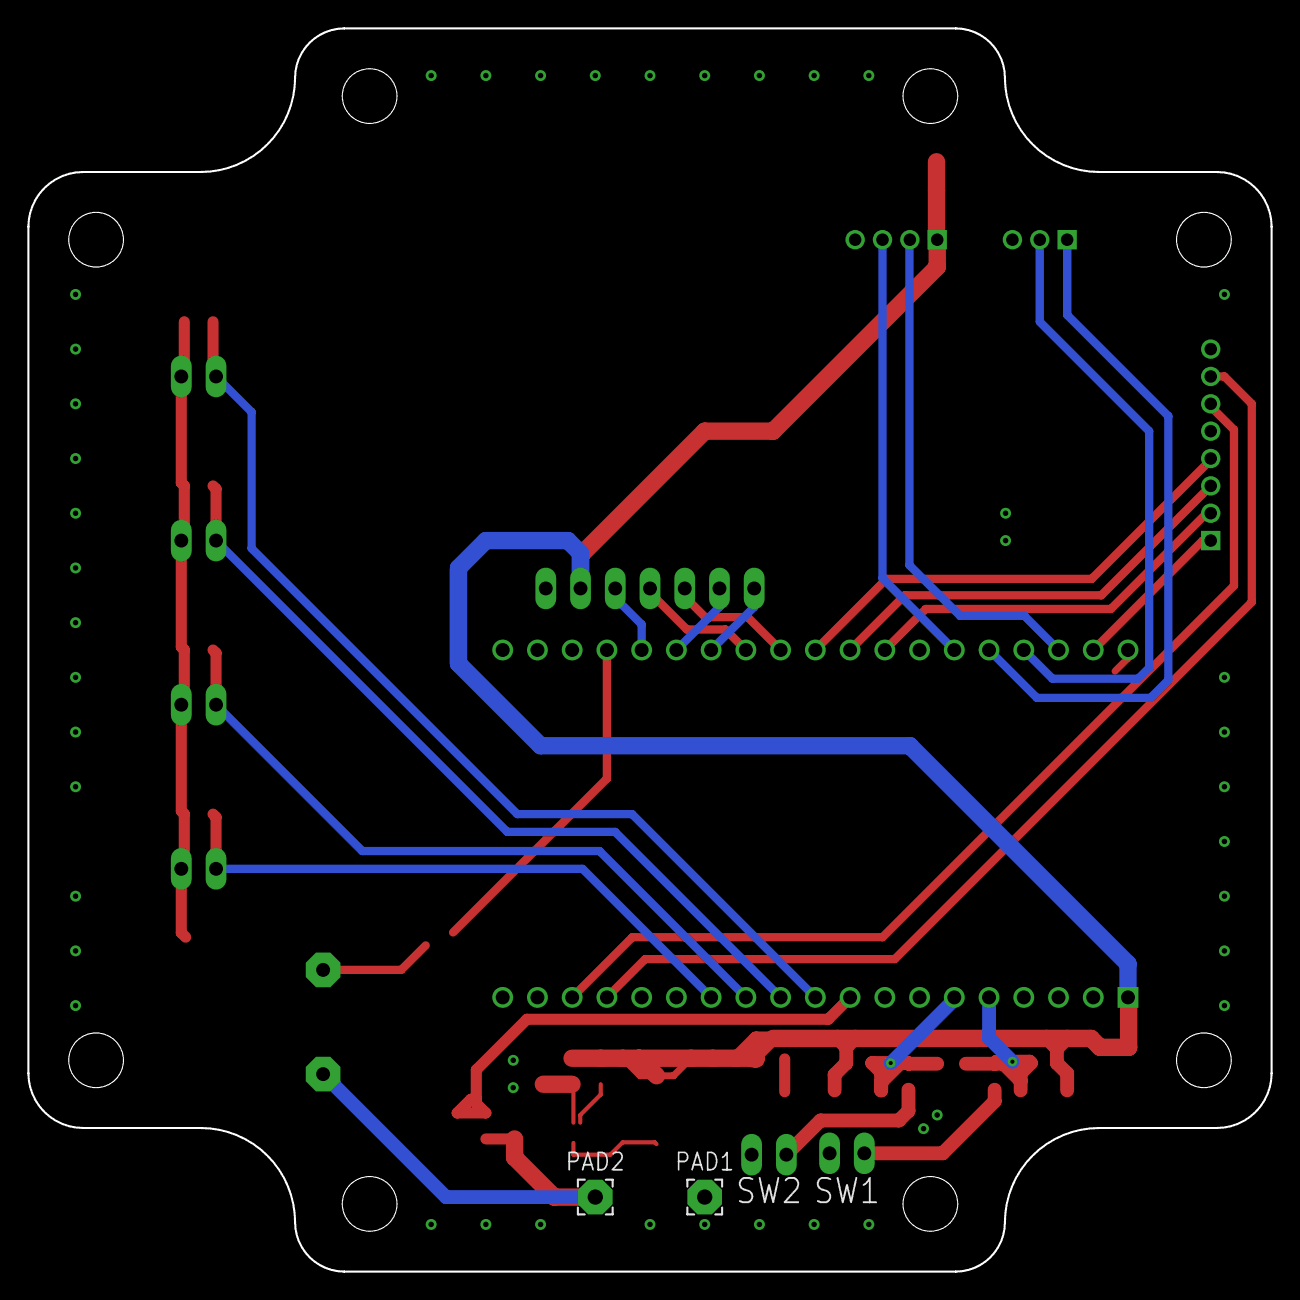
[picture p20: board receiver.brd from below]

Board: 2 copper layers, 90.9 x 90.9 mm, 43 parts (2 on the bottom side), 34 nets.

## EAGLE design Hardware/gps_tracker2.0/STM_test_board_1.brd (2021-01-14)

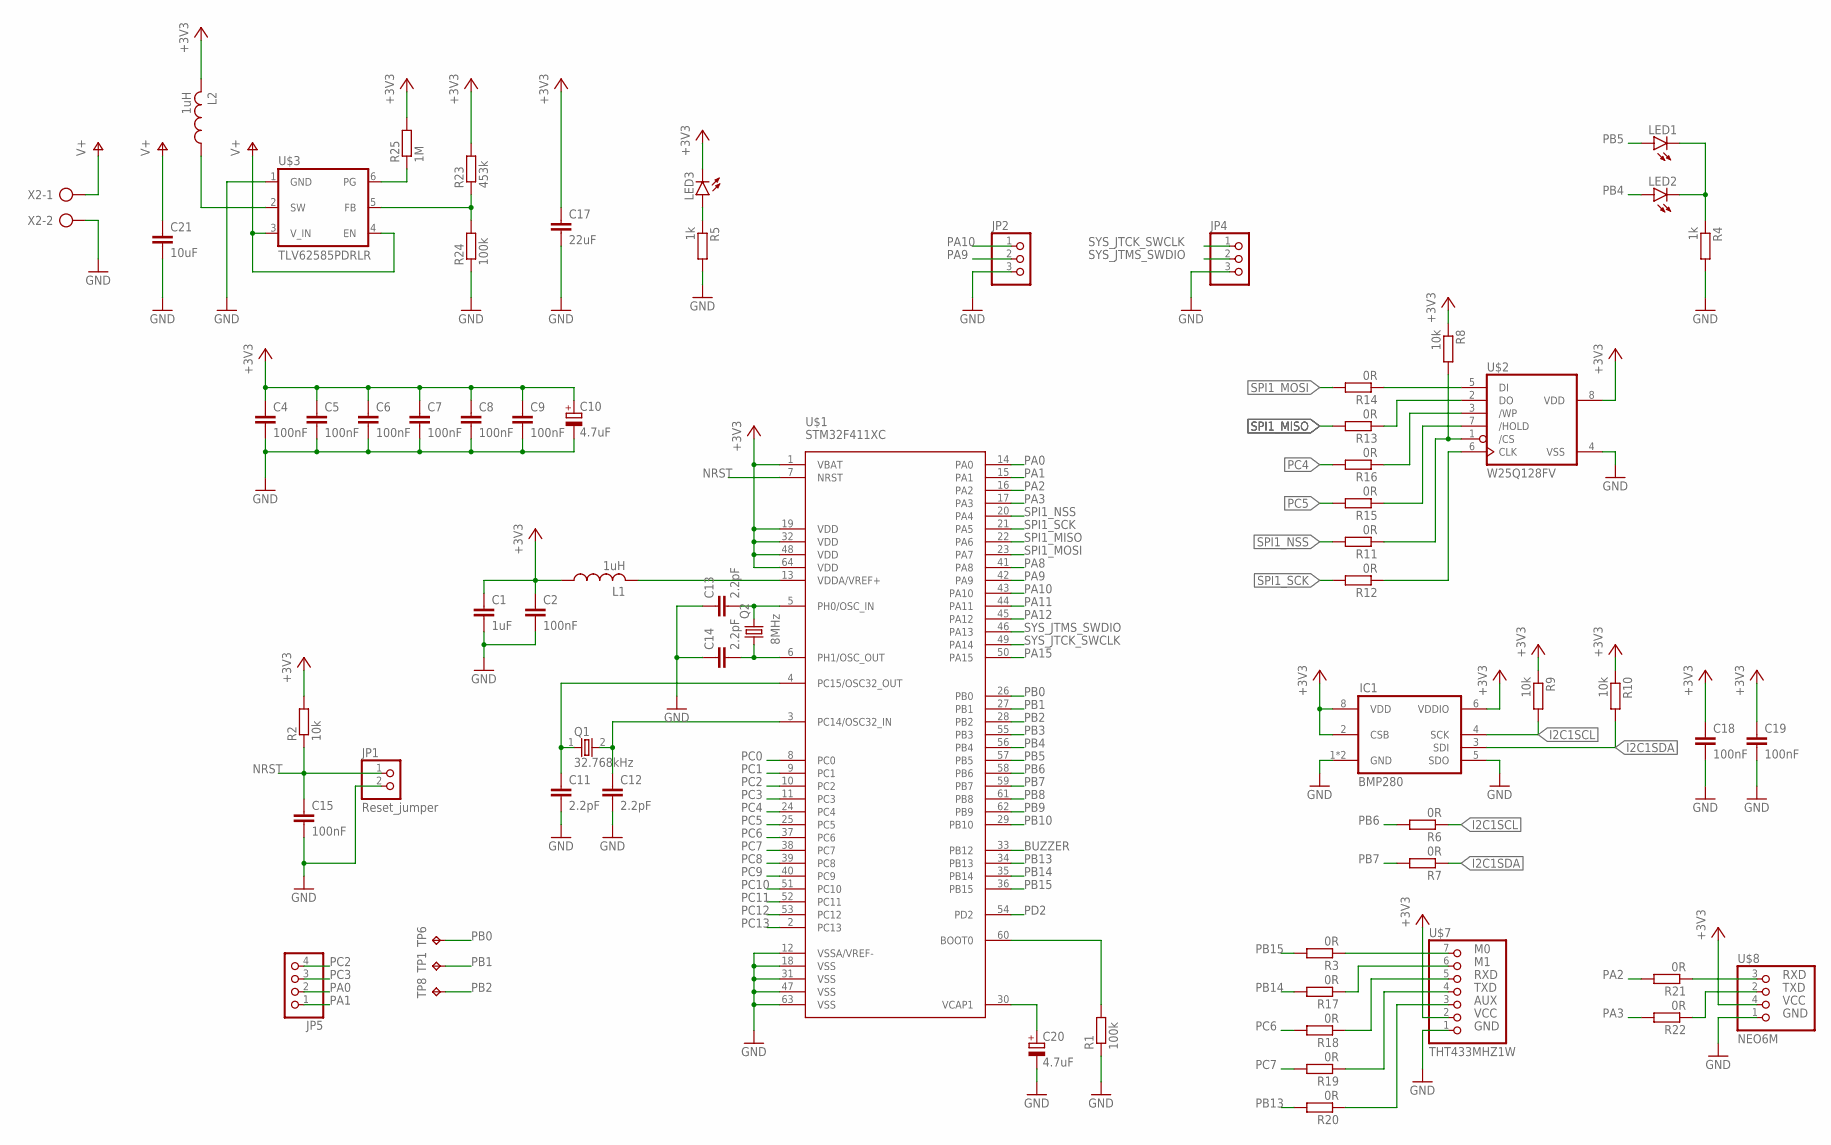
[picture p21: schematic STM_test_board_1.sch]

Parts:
C1: 1uF; C1206
C2, C4, C5, C6, C7, C8, C9, C15, C18, C19: 100nF; C0805
C10, C20: 4.7uF; CT3216
C11, C12, C13, C14: 2.2pF; C0805
C17: 22uF; C1206
C21: 10uF; C0805
IC1: BMP280
JP1: Reset_jumper; 1X02
JP2, JP4: PINHD-1X3M; 1X03M
JP5: PINHD-1X4M; 1X04M
L1: 1uH; 0207/7
L2: 1uH; L5650M
LED1, LED2, LED3: LEDSMT1206; 1206
Q1: 32.768kHz; MA507
Q2: 8MHz; CTS406
R1, R24: 100k; R0805
R2, R8, R9, R10: 10k; R0805
R3, R6, R7, R11, R12, R13, R14, R15, R16, R17, R18, R19, R20, R21, R22: 0R; R0805
R4, R5: 1k; R0805
R23: 453k; R1206
R25: 1M; R1206
TP1, TP6, TP8: TPTP20SQ; TP20SQ
U$1: STM32F411XC; LQFP64
U$2: W25Q128FV; TSSOP-8
U$3: TLV62585PDRLR; SOT563
U$7: THT433MHZ1W; E32M1000
U$8: NEO6M; 1X04
X2: AK300/2

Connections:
+3V3: C1.1, C2.1, C4.1, C5.1, C6.1, C7.1, C8.1, C9.1, C10.+, C17.1, C18.1, C19.1, IC1.2 (CSB), IC1.6 (VDDIO), IC1.8 (VDD), L1.1, L2.2, LED3.C, R2.2, R8.1, R9.1, R10.1, R23.2, R25.2, U$1.1 (VBAT), U$1.19 (VDD), U$1.32 (VDD), U$1.48 (VDD), U$1.64 (VDD), U$2.8 (VDD), U$7.2 (VCC), U$8.4 (VCC)
BUZZER: U$1.33 (PB12)
GND: C1.2, C2.2, C4.2, C5.2, C6.2, C7.2, C8.2, C9.2, C10.-, C11.2, C12.2, C13.1, C14.1, C15.2, C17.2, C18.2, C19.2, C20.-, C21.2, IC1.1 (GND), IC1.5 (SDO), IC1.7 (GND), JP1.2, JP2.3, JP4.3, R1.1, R4.2, R5.2, R24.1, U$1.12 (VSSA/VREF-), U$1.18 (VSS), U$1.31 (VSS), U$1.47 (VSS), U$1.63 (VSS), U$2.4 (VSS), U$3.1 (GND), U$7.1 (GND), U$8.1 (GND), X2.2
I2C1SCL: IC1.4 (SCK), R6.1, R9.2
I2C1SDA: IC1.3 (SDI), R7.1, R10.2
unnamed: C13.2, Q2.3 (2), U$1.5 (PH0/OSC_IN)
unnamed: C20.+, U$1.30 (VCAP1)
unnamed: C12.1, Q1.2, U$1.3 (PC14/OSC32_IN)
unnamed: C11.1, Q1.1, U$1.4 (PC15/OSC32_OUT)
unnamed: C14.2, Q2.1, U$1.6 (PH1/OSC_OUT)
unnamed: R1.2, U$1.60 (BOOT0)
unnamed: L1.2, U$1.13 (VDDA/VREF+)
unnamed: R14.1, U$2.5 (DI)
unnamed: R13.1, U$2.2 (DO)
unnamed: R12.1, U$2.6 (CLK)
unnamed: R16.1, U$2.3 (/WP)
unnamed: R15.1, U$2.7 (/HOLD)
unnamed: R3.1, U$7.7 (M0)
unnamed: R8.2, R11.1, U$2.1 (/CS)
unnamed: R17.1, U$7.6 (M1)
unnamed: R18.1, U$7.5 (RXD)
unnamed: R19.1, U$7.4 (TXD)
unnamed: R20.1, U$7.3 (AUX)
unnamed: R21.1, U$8.3 (RXD)
unnamed: LED1.C, LED2.C, R4.1
unnamed: LED3.A, R5.1
unnamed: R22.1, U$8.2 (TXD)
unnamed: R23.1, R24.2, U$3.5 (FB)
unnamed: R25.1, U$3.6 (PG)
unnamed: L2.1, U$3.2 (SW)
NRST: C15.1, JP1.1, R2.1, U$1.7 (NRST)
PA0: JP5.2, U$1.14 (PA0)
PA1: JP5.1, U$1.15 (PA1)
PA2: R21.2, U$1.16 (PA2)
PA3: R22.2, U$1.17 (PA3)
PA8: U$1.41 (PA8)
PA9: JP2.2, U$1.42 (PA9)
PA10: JP2.1, U$1.43 (PA10)
PA11: U$1.44 (PA11)
PA12: U$1.45 (PA12)
PA15: U$1.50 (PA15)
PB0: TP6.TP, U$1.26 (PB0)
PB1: TP1.TP, U$1.27 (PB1)
PB2: TP8.TP, U$1.28 (PB2)
PB3: U$1.55 (PB3)
PB4: LED2.A, U$1.56 (PB4)
PB5: LED1.A, U$1.57 (PB5)
PB6: R6.2, U$1.58 (PB6)
PB7: R7.2, U$1.59 (PB7)
PB8: U$1.61 (PB8)
PB9: U$1.62 (PB9)
PB10: U$1.29 (PB10)
PB13: R20.2, U$1.34 (PB13)
PB14: R17.2, U$1.35 (PB14)
PB15: R3.2, U$1.36 (PB15)
PC0: U$1.8 (PC0)
PC1: U$1.9 (PC1)
PC2: JP5.4, U$1.10 (PC2)
PC3: JP5.3, U$1.11 (PC3)
PC4: R16.2, U$1.24 (PC4)
PC5: R15.2, U$1.25 (PC5)
PC6: R18.2, U$1.37 (PC6)
PC7: R19.2, U$1.38 (PC7)
PC8: U$1.39 (PC8)
PC9: U$1.40 (PC9)
PC10: U$1.51 (PC10)
PC11: U$1.52 (PC11)
PC12: U$1.53 (PC12)
PC13: U$1.2 (PC13)
PD2: U$1.54 (PD2)
SPI1_MISO: R13.2, U$1.22 (PA6)
SPI1_MOSI: R14.2, U$1.23 (PA7)
SPI1_NSS: R11.2, U$1.20 (PA4)
SPI1_SCK: R12.2, U$1.21 (PA5)
SYS_JTCK_SWCLK: JP4.1, U$1.49 (PA14)
SYS_JTMS_SWDIO: JP4.2, U$1.46 (PA13)
V+: C21.1, U$3.3 (V_IN), U$3.4 (EN), X2.1

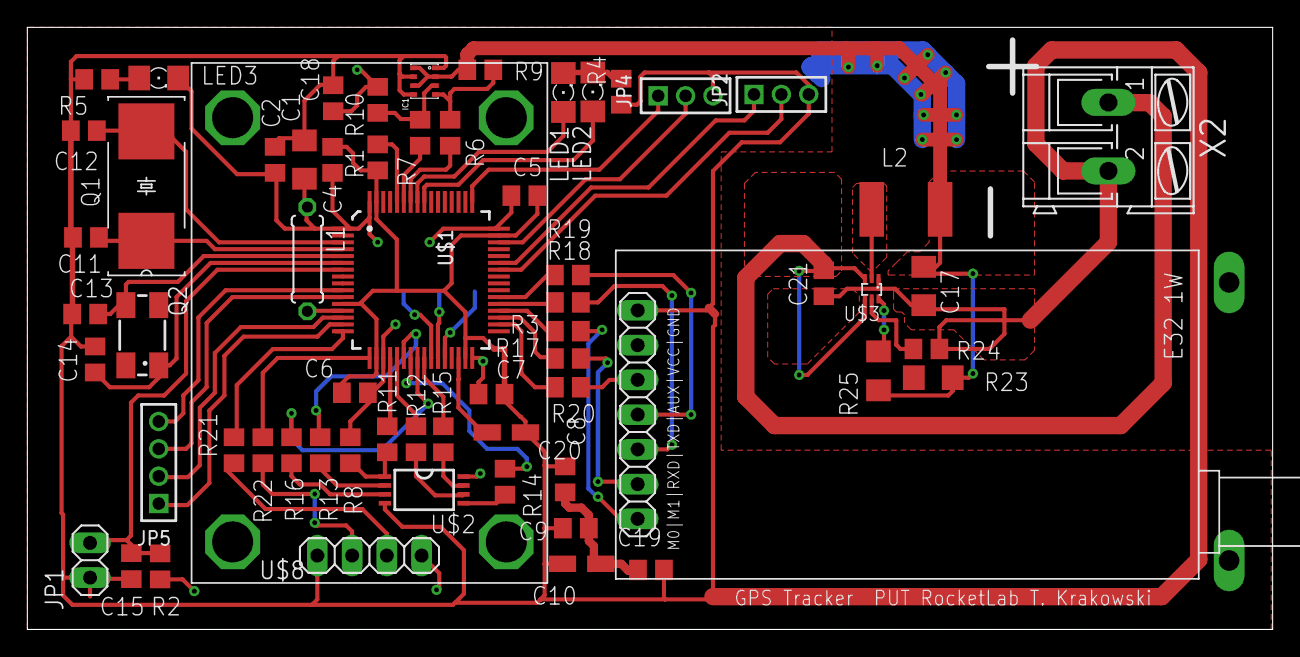
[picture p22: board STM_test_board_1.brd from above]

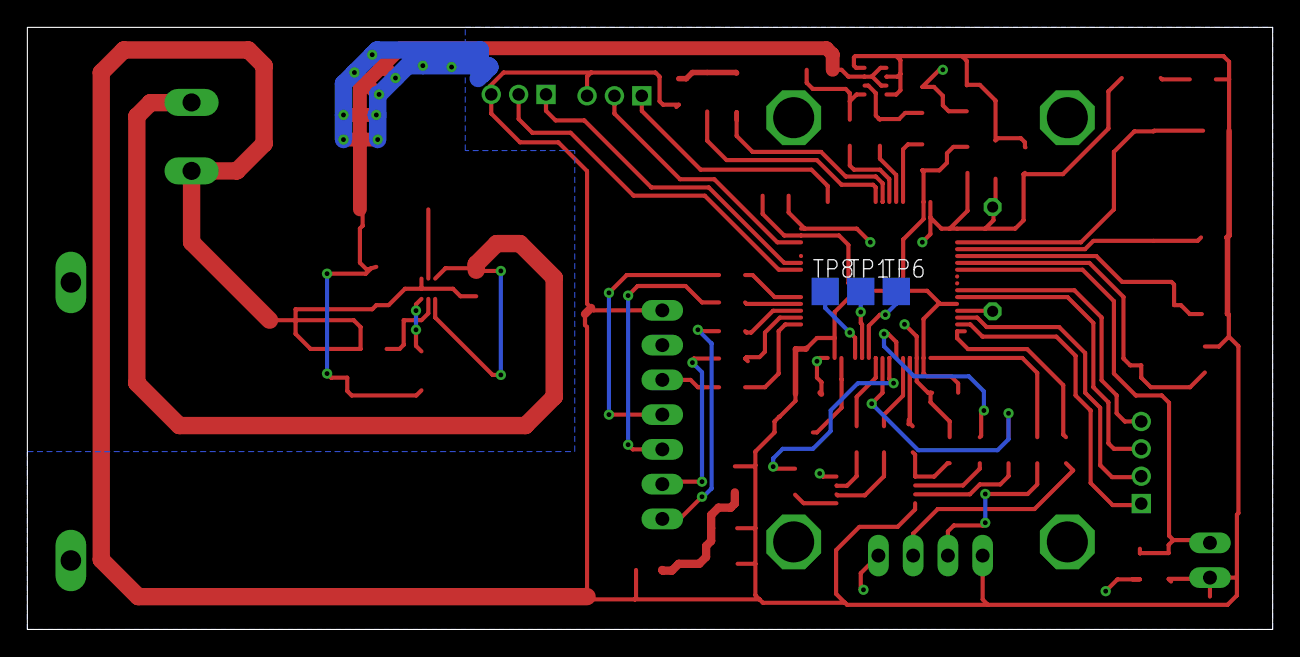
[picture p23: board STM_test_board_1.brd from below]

Board: 2 copper layers, 91.0 x 44.0 mm, 65 parts (3 on the bottom side), 59 nets.

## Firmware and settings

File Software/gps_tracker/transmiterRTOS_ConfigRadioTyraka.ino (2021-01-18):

#include <STM32FreeRTOS.h>
#include "queue.h"
// #include <RH_E32.h>
#include <RadioTyraka.h>
#include <TinyGPS++.h>
#include <EEPROM.h>
#include <ArduinoJson.h>
// #include "Logger.h"
#include "logParser.h"
#include "LoraStructs.h"
#include "FlashSPI.h"
#include "barometric_formula.h"
#include <Adafruit_BMP280.h>

//Define configuration interupt
#define configInterupt PB15

//Define led pins
#define led1 PB0  //error
#define led2 PB1  // setup done
#define led3 PB2  // lora init done
#define led4 PB10 // flesh write

// Define lora pins
#define tx PA9
#define rx PA10
#define m0 PA11
#define m1 PA12
#define aux PC13

// define flash pins:
#define flashCs PA8
//#define flashMiso PA6
//#define flashMosi PA7
//#define flashWp PC4
//#define flashHold PA4
//#define clk PA5

// define bmp280 pins
#define sda PB7
#define scl PB6

// inicialize queue for BMP Task
QueueHandle_t xQueue_Pressure;
QueueHandle_t xQueue_Temp;
QueueHandle_t xQueue_Altitude;
// inicialize queue for GPS Task
QueueHandle_t xQueue_GpsLat;
QueueHandle_t xQueue_GpsLon;
QueueHandle_t xQueue_GpsHour;
QueueHandle_t xQueue_GpsMinute;
QueueHandle_t xQueue_GpsSecond;
// inicialize queue for Logger Task
QueueHandle_t xQueue_Logger;

// Define Hardware Serials:
HardwareSerial logSerial(PC7, PC6); // RX, TX
// Logger logger(&logSerial);                 // Logger inicialization
FlashSPI flash(&logSerial); // Flash inicialization
//-----------------------------------------------------------------------------------

// gpsSerial - gps comunication
HardwareSerial gpsSerial(USART2);
TinyGPSPlus gps;
//-----------------------------------------------------------------------------------

// loraSerial - lora comunication
HardwareSerial loraSerial(rx, tx);
RadioTyraka driver(&loraSerial, m0, m1, aux, 127);
// RH_E32 driver(&loraSerial, m0, m1, aux); //M0,M1,AUX
//-----------------------------------------------------------------------------------

// bmp280 pressure sensor inicialization
Adafruit_BMP280 bmp; // use I2C interface
Adafruit_Sensor *bmp_temp = bmp.getTemperatureSensor();
Adafruit_Sensor *bmp_pressure = bmp.getPressureSensor();

sensors_event_t temp_event, pressure_event;
//-----------------------------------------------------------------------------------

// trucker configuration
typedef struct TruckerConfig
{
    uint16_t dataRate;
    uint16_t frequency;
    uint16_t power;
};

TruckerConfig trackerConfig;

int eeAddress = 0; //EEPROM address to start reading from

const byte numChars = 32;
char receivedChars[numChars];
char tempChars[numChars]; // temporary array for use when parsing

boolean newData = false;
boolean configBool;

const size_t capacity = JSON_OBJECT_SIZE(3);
DynamicJsonDocument doc(capacity);
//-----------------------------------------------------------------------------------

// Lora tracker packet
// TRACKER_PACKET dataFrame;
//-----------------------------------------------------------------------------------

void setup()
{
    //  ----------SETUP SERIAL-------------
    logSerial.begin(115200);
    while (!gpsSerial)
        ;
    logSerial.println("logSerial begin");

    gpsSerial.begin(9600);
    while (!gpsSerial)
        ;
    logSerial.println("gpsSerial begin");

    loraSerial.begin(9600);
    while (!loraSerial)
        ;
    logSerial.println("loraSerial begin");
    //---------------------------------------------------------------------------

    //  Inicialize pinMode for leds
    pinMode(led1, OUTPUT);
    //    logger.info(F("setup"), "led1 - error set to pin " + String(led1, DEC));
    pinMode(led2, OUTPUT);
    //    logger.info(F("setup"), "led2 - setup done set to pin " + String(led2, DEC));
    pinMode(led3, OUTPUT);
    //    logger.info(F("setup"), "led3 - init success set to pin " + String(led3, DEC));
    pinMode(led4, OUTPUT);
    //    logger.info(F("setup"), "led4 - flesh write set to pin " + String(led4, DEC));
    //---------------------------------------------------------------------------

    // Begin BMP280 I2C
    Wire.setSDA(sda);
    Wire.setSCL(scl);
    Wire.begin();

    // BMP280 setup
    if (!bmp.begin(0x76))
    {
        logSerial.println(F("Could not find a valid BMP280 sensor, check wiring!"));
        digitalWrite(led1, HIGH);
        while (1)
            delay(10);
    }

    bmp.setSampling(Adafruit_BMP280::MODE_NORMAL,     /* Operating Mode. */
                    Adafruit_BMP280::SAMPLING_X2,     /* Temp. oversampling */
                    Adafruit_BMP280::SAMPLING_X16,    /* Pressure oversampling */
                    Adafruit_BMP280::FILTER_X16,      /* Filtering. */
                    Adafruit_BMP280::STANDBY_MS_500); /* Standby time. */

    //-----------------------------------------------------------------------------------

    // Flash setup
    logSerial.println("Attempting to initialize flash memory.");
    while (!flash.beginFlash(flashCs))
    {
        logSerial.println("Error: Flash initialization fail!");
        delay(500);
    }
    //-----------------------------------------------------------------------------------

    // lora setup
    if (!driver.init())
    {
        //        logger.error(F("setup"), F("init failed"));
        logSerial.println("init failed");
        digitalWrite(led1, HIGH);
        while (1)
            ;
    }

    // lora manuall configuration
    //    if (!driver.setDataRate(RH_E32::DataRate2kbps)) // 1kbps, 2kbps, 5kbps, 8kbps, 10kbps, 15kbps, 20kbps, 25kbps
    //        logSerial.println("setDataRate failed");
    //    if (!driver.setPower(RH_E32::Power21dBm)) //21dBm, 24dBm, 27dBm, 30dBm
    //        logSerial.println("setPower failed");
    //    if (!driver.setFrequency(411)) // 410 < uint16_t < 441
    //        logSerial.println("setFrequency failed");

    // lora configuration via TyrakaApp
    readConfig();
    showJSONData();
    resolveConfig();
    //---------------------------------------------------------------------------

    digitalWrite(led3, HIGH); //led for init compleat

    if (digitalRead(configInterupt) == LOW)
    {
        config(); // tracker configuration
    }

    // Create queue for BMP Task
    xQueue_Altitude = xQueueCreate(1, sizeof(float));
    xQueue_Pressure = xQueueCreate(1, sizeof(float));
    xQueue_Temp = xQueueCreate(1, sizeof(float));
    // Create queue for GPS Task
    xQueue_GpsLat = xQueueCreate(1, sizeof(float));
    xQueue_GpsLon = xQueueCreate(1, sizeof(float));
    xQueue_GpsHour = xQueueCreate(1, sizeof(float));
    xQueue_GpsMinute = xQueueCreate(1, sizeof(float));
    xQueue_GpsSecond = xQueueCreate(1, sizeof(float));
    // Create queue for Loggger Task
    xQueue_Logger = xQueueCreate(5, sizeof(char *));

    logSerial.println("Kolejki iniit");

    // RTOS TASK CREATION
    xTaskCreate(vBmp280ControllerTask, "BMP 280 CONTROLLER TASK", 128, NULL, 1, NULL);
    xTaskCreate(vGpsControllerTask, "GPS CONTROLLER TASK", 128, NULL, 1, NULL);
    xTaskCreate(vFlashControllerTask, "FLASH CONTROLLER TASK", 128, NULL, 1, NULL);
    xTaskCreate(vLoraControllerTask, "LORA CONTROLLER TASK", 128, NULL, 1, NULL);
    xTaskCreate(vLoggerTask, "LOGGER TASK", 128, NULL, 1, NULL);

    // start scheduler
    vTaskStartScheduler();
    logSerial.println("Insufficient RAM");
    while (1)
        ;
}

void loop()
{
}

void vBmp280ControllerTask(void *pvParameters)
{

    float pressure = 0;
    float altitude = 0;
    float sum = 0;
    float temperature = 0;
    float sea_lvl_pres = 1011.45;
    char bmpChar[25];
    char *msg;
    //    String data = "";

    bmp_pressure->getEvent(&pressure_event);

    for (int i = 0; i < 100; i++)
    {
        sum = sum + pressure_event.pressure;
        bmp_pressure->getEvent(&pressure_event);
    }
    sea_lvl_pres = sum / 100;
    //        logSerial.println(sea_lvl_pres);

    while (1)
    {
        bmp_temp->getEvent(&temp_event);
        bmp_pressure->getEvent(&pressure_event);

        pressure = pressure_event.pressure;
        temperature = temp_event.temperature;
        altitude = barinetricAltitude(pressure, temperature, sea_lvl_pres);

        xQueueOverwrite(xQueue_Pressure, &pressure);
        xQueueOverwrite(xQueue_Temp, &temperature);
        xQueueOverwrite(xQueue_Altitude, &altitude);

        msg = debug("BMP TASK", "bmp data collected");
        xQueueSend(xQueue_Logger, &(msg), portMAX_DELAY);
        //
        vTaskDelay(pdMS_TO_TICKS(100));
    }
}

void vFlashControllerTask(void *pvParameters)
{
    // flash setup
    float bmpPressure, bmpTemperature, bmpAltitude;
    float gpsLat, gpsLon, gpsHour, gpsMinute, gpsSecond;
    int counter = 0;
    float mtime = 0;
    char data[128];
    int startTime = millis();
    char *msg;
    String dataString, label, gpsString, bmpString;

    flash.writeFlash("counter,miliseconds,latitude,longitude,timeUTC,pressure,temperature,altitude", 77);

    while (1) // A Task shall never return or exit.
    {
        if (xQueuePeek(xQueue_GpsLat, &(gpsLat), (TickType_t)5) == pdFALSE)
        {
            gpsLat = -1;
        }
        if (xQueuePeek(xQueue_GpsLon, &(gpsLon), (TickType_t)5) == pdFALSE)
        {
            gpsLon = -1;
        }
        if (xQueuePeek(xQueue_GpsHour, &(gpsHour), (TickType_t)5) == pdFALSE)
        {
            gpsHour = -1;
        }
        if (xQueuePeek(xQueue_GpsMinute, &(gpsMinute), (TickType_t)5) == pdFALSE)
        {
            gpsMinute = -1;
        }
        if (xQueuePeek(xQueue_GpsSecond, &(gpsSecond), (TickType_t)5) == pdFALSE)
        {
            gpsSecond = -1;
        }
        if (xQueuePeek(xQueue_Pressure, &(bmpPressure), (TickType_t)5) == pdFALSE)
        {
            bmpPressure = -1;
        }
        if (xQueuePeek(xQueue_Temp, &(bmpTemperature), (TickType_t)5) == pdFALSE)
        {
            bmpTemperature = -1;
        }
        if (xQueuePeek(xQueue_Altitude, &(bmpAltitude), (TickType_t)5) == pdFALSE)
        {
            bmpAltitude = -1;
        }

        mtime = (float)(millis() - startTime) / 1000;

        label = String(counter++, DEC) + "," + String(mtime, DEC);
        gpsString = String(gpsLat, DEC) + "," + String(gpsLon, DEC) + "," + String(gpsHour) + ":" + String(gpsMinute) + ":" + String(gpsSecond);
        bmpString = String(bmpPressure, DEC) + "," + String(bmpTemperature, DEC) + "," + String(bmpAltitude, DEC);
        dataString = label + "," + gpsString + "," + bmpString;

        dataString.toCharArray(data, sizeof(data));

        flash.writeFlash(data, strlen(data) + 1);
        msg = debug("FLASH TASK", "DATA SAVE !!!!");
        xQueueSend(xQueue_Logger, &(msg), portMAX_DELAY);
        vTaskDelay(pdMS_TO_TICKS(100));
    }
}

void vGpsControllerTask(void *pvParameters)
{
    // GPS Setup
    float gpsLat, gpsLon;
    int gpsHour, gpsMinute, gpsSecond;
    char *gpsChar;
    char *msg;

    while (1)
    {
        while (gpsSerial.available() > 0)
            if (gps.encode(gpsSerial.read()))
            {
                if (gps.location.isValid())
                {
                    gpsLat = gps.location.lat();
                    gpsLon = gps.location.lng();
                    gpsHour = gps.time.hour();
                    gpsMinute = gps.time.minute();
                    gpsSecond = gps.time.second();
                    xQueueOverwrite(xQueue_GpsLat, &gpsLat);
                    xQueueOverwrite(xQueue_GpsLon, &gpsLon);
                    xQueueOverwrite(xQueue_GpsHour, &gpsHour);
                    xQueueOverwrite(xQueue_GpsMinute, &gpsMinute);
                    xQueueOverwrite(xQueue_GpsSecond, &gpsSecond);

                    msg = debug("GPS TASK", "FIX AVAIABLE !!!!");
                    xQueueSend(xQueue_Logger, &(msg), portMAX_DELAY);
                }
                else
                {
                    msg = debug("GPS TASK", "FIX NOT AVAIABLE !!!!");
                    xQueueSend(xQueue_Logger, &(msg), portMAX_DELAY);
                }
            }
        // vTaskDelay(1);
        vTaskDelay(pdMS_TO_TICKS(100));
    }
}

void vLoraControllerTask(void *pvParameters)
{
    struct TRACKER_PACKET dataFrame;
    char send_data[RH_E32_MAX_MESSAGE_LEN];
    char *msg;

    while (1)
    {
        if (xQueuePeek(xQueue_GpsLat, &(dataFrame.gpsLat), (TickType_t)5) == pdFALSE)
        {
            dataFrame.gpsLat = -1;
        }
        if (xQueuePeek(xQueue_GpsLon, &(dataFrame.gpsLon), (TickType_t)5) == pdFALSE)
        {
            dataFrame.gpsLon = -1;
        }
        if (xQueuePeek(xQueue_GpsHour, &(dataFrame.gpsHour), (TickType_t)5) == pdFALSE)
        {
            dataFrame.gpsHour = -1;
        }
        if (xQueuePeek(xQueue_GpsMinute, &(dataFrame.gpsMinute), (TickType_t)5) == pdFALSE)
        {
            dataFrame.gpsMinute = -1;
        }
        if (xQueuePeek(xQueue_GpsSecond, &(dataFrame.gpsSecond), (TickType_t)5) == pdFALSE)
        {
            dataFrame.gpsSecond = -1;
        }
        if (xQueuePeek(xQueue_Pressure, &(dataFrame.bmpPressure), (TickType_t)5) == pdFALSE)
        {
            dataFrame.bmpPressure = -1;
        }
        if (xQueuePeek(xQueue_Temp, &(dataFrame.bmpTemperature), (TickType_t)5) == pdFALSE)
        {
            dataFrame.bmpTemperature = -1;
        }
        if (xQueuePeek(xQueue_Altitude, &(dataFrame.bmpAltitude), (TickType_t)5) == pdFALSE)
        {
            dataFrame.bmpAltitude = -1;
        }

        dataFrame.counter++;
        Status status = driver.sendStruct(&dataFrame, sizeof(dataFrame));

        if (status == L_SUCCESS) // check if Status of transmition is successful.
        {
            msg = ok("LORA TASK", "packet send !!!!");
            xQueueSend(xQueue_Logger, &(msg), portMAX_DELAY);
        }
        else
        {
            msg = error("LORA TASK", "packet not send !!!!");
            xQueueSend(xQueue_Logger, &(msg), portMAX_DELAY);
        }
    }
}

void vLoggerTask(void *pvParameters)
{
    char *pcMsgToPrint;
    while (1)
    {
        xQueueReceive(xQueue_Logger, &pcMsgToPrint, portMAX_DELAY);
        logSerial.println(pcMsgToPrint);
    }
}
//---------------------------------------------------------------------------

// Function to confugure tracker by uart
void config()
{
    // logSerial.println(F("lora configuration"));
    // logSerial.println(F("Enter data in this style <dataRate,frequency,power>"));
    // logSerial.println(F("Example: <10,411,30>"));
    // logSerial.println(F("Default: <5,433,21>"));
    // logSerial.println(F("Current configuration settings: "));
    // readConfig();
    configBool = true;
    while (configBool)
    {
        if (logSerial.available() > 0)
        {
            String msg = logSerial.readString();
            msg.trim();
            // logSerial.println(msg);

            if (msg.startsWith("readConfig"))
            {
                readConfig();
            }
            else if (msg.startsWith("writeConfig"))
            {
                msg.remove(0, strlen("writeConfig") + 1); // Get parameters
                msg.toCharArray(receivedChars, numChars); // Copy String to char array
                receivedChars[msg.length() + 1] = '\0';   // Terminate the string

                // this temporary copy is necessary to protect the original data
                // because strtok() used in parseData() replaces the commas with \0
                strcpy(tempChars, receivedChars);

                parseData(); // split the data into its parts

                EEPROM.put(eeAddress, trackerConfig); // Saving data to flesh/eeproom
                // EEPROM.commit();     // only use for esp32

                showJSONData();

                resolveConfig();
            }
            else if (msg.startsWith("eraseAll"))
            {
                logSerial.println("Erase flash started");
                digitalWrite(led4, HIGH);
                flash.eraseAll();
                digitalWrite(led4, LOW);
                Serial.println("Flash erased");
            }
            else if (msg.startsWith("listFiles"))
            {
                flash.listFiles();
            }
            else if (msg.startsWith("readFile"))
            {
                msg.remove(0, strlen("readFile") + 1);    // Get parameters
                msg.toCharArray(receivedChars, numChars); // Copy String to char array
                receivedChars[msg.length() + 1] = '\0';   // Terminate the string

                // this temporary copy is necessary to protect the original data
                // because strtok() used in parseData() replaces the commas with \0
                strcpy(tempChars, receivedChars);
                logSerial.print("Read: ");
                logSerial.println(tempChars);
                flash.readFile(tempChars);
            }
            else if (msg.startsWith("endConfig"))
            {
                configBool = false;
                Serial.println("Config ended");
            }
            else
            {
                logSerial.println("Command not found: " + msg);
            }
            logSerial.println("|");
        }
    }
    logSerial.println("Tracker configuration complete");
}
//---------------------------------------------------------------------------

// Function to read and show tracker configuration
void readConfig()
{
    EEPROM.get(eeAddress, trackerConfig);
    showJSONData();
}
//---------------------------------------------------------------------------

// Function to resolve lora configuration
void resolveConfig()
{
    // Lora config
    // Defaultowe wartości po inicjalizacji
    // 433MHz, 21dBm, 5kbps

    // Set DataRate
    // 1kbps, 2kbps, 5kbps, 8kbps, 10kbps, 15kbps, 20kbps, 25kbps
    switch (trackerConfig.dataRate)
    {
    case 1:
        logSerial.println(F("setDataRate 1kbps"));
        if (!driver.setDataRate(RH_E32::DataRate1kbps))
            logSerial.println(F("setDataRate failed"));
        break;
    case 2:
        logSerial.println(F("setDataRate 2kbps"));
        if (!driver.setDataRate(RH_E32::DataRate2kbps))
            logSerial.println(F("setDataRate failed"));
        break;
    case 5:
        logSerial.println(F("setDataRate 5kbps"));
        if (!driver.setDataRate(RH_E32::DataRate5kbps))
            logSerial.println(F("setDataRate failed"));
        break;
    case 8:
        logSerial.println(F("setDataRate 8kbps"));
        if (!driver.setDataRate(RH_E32::DataRate8kbps))
            logSerial.println(F("setDataRate failed"));
        break;
    case 10:
        logSerial.println(F("setDataRate 10kbps"));
        if (!driver.setDataRate(RH_E32::DataRate10kbps))
            logSerial.println(F("setDataRate failed"));
        break;
    case 15:
        logSerial.println(F("setDataRate 15kbps"));
        if (!driver.setDataRate(RH_E32::DataRate15kbps))
            logSerial.println(F("setDataRate failed"));
        break;
    case 20:
        logSerial.println(F("setDataRate 20kbps"));
        if (!driver.setDataRate(RH_E32::DataRate20kbps))
            logSerial.println(F("setDataRate failed"));
        break;
    case 25:
        logSerial.println(F("setDataRate 25kbps"));
        if (!driver.setDataRate(RH_E32::DataRate25kbps))
            logSerial.println(F("setDataRate failed"));
        break;
    default:
        logSerial.println(F("setDataRate default 5kbps"));
        if (!driver.setDataRate(RH_E32::DataRate5kbps))
            logSerial.println(F("setDataRate failed"));
        break;
    }
    //---------------------------------------------------------------------------

    // Set Power
    //21dBm, 24dBm, 27dBm, 30dBm
    switch (trackerConfig.power)
    {
    case 21:
        logSerial.println(F("setPower 21dBm"));
        if (!driver.setPower(RH_E32::Power21dBm))
            logSerial.println(F("setPower failed"));
        break;
    case 24:
        logSerial.println(F("setPower 24dBm"));
        if (!driver.setPower(RH_E32::Power24dBm))
            logSerial.println(F("setPower failed"));
        break;
    case 27:
        logSerial.println(F("setPower 27dBm"));
        if (!driver.setPower(RH_E32::Power27dBm))
            logSerial.println(F("setPower failed"));
        break;
    case 30:
        logSerial.println(F("setPower 30dBm"));
        if (!driver.setPower(RH_E32::Power30dBm))
            logSerial.println(F("setPower failed"));
        break;
    default:
        logSerial.println(F("setPower default 21dBm"));
        if (!driver.setPower(RH_E32::Power21dBm))
            logSerial.println(F("setPower failed"));
        break;
    }
    //---------------------------------------------------------------------------

    // Set Frequency
    // 410 < uint16_t < 441
    if (trackerConfig.frequency < 410 || trackerConfig.frequency > 441)
    {
        logSerial.println(F("setFrequency no valid frequancy set to deafult 433"));
        if (!driver.setFrequency(433))
            logSerial.println(F("setFrequency failed"));
    }
    else
    {
        logSerial.print(F("setFrequency "));
        logSerial.println(trackerConfig.frequency);
        if (!driver.setFrequency(trackerConfig.frequency)) // 410 < uint16_t < 441
            logSerial.println(F("setFrequency failed "));
    }
}
//---------------------------------------------------------------------------

// Function to parse date from recived configuraton
// data are assign to trackerConfig
void parseData()
{ // split the data into its parts

    char *strtokIndx; // this is used by strtok() as an index

    strtokIndx = strtok(tempChars, ",");                 // get the first part - the string
    trackerConfig.dataRate = (uint16_t)atoi(strtokIndx); //    strcpy(messageFromPC, strtokIndx);   // copy it to messageFromPC

    strtokIndx = strtok(NULL, ",");                       // this continues where the previous call left off
    trackerConfig.frequency = (uint16_t)atoi(strtokIndx); // convert this part to an integer

    strtokIndx = strtok(NULL, ",");
    trackerConfig.power = (uint16_t)atoi(strtokIndx); // convert this part to a float
}
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

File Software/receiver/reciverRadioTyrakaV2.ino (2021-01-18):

#include <EEPROM.h>
// #include <RH_E32.h>
#include <RadioTyraka.h>
#include "LoraStructs.h"
#include "Logger.h"
#include <ArduinoJson.h>

// define buttons pins
#define sw1 34
#define sw2 35

// define leds pins
#define led1 26 //error
#define led2 27 // setup done
#define led3 12 // lora init done
#define led4 14 // flesh write

// define lora pins
// Lora pins
#define loraRx 17
#define loraTx 16
#define m0 4
#define m1 0
#define aux 2

// lora configuration struct
struct LoraConfig
{
    uint16_t dataRate;
    uint16_t frequency;
    uint16_t power;
};

// Logger inicialization
Logger logger(&Serial);

// Lora inicialization
// RH_E32 driver(&Serial2, m0, m1, aux); //M0,M1,AUX
RadioTyraka driver(&Serial2, m0, m1, aux);

// TRACKER_PACKET incomingData; // Lora packet for tracker

LoraConfig loraConfig; //Lora configuration

const size_t capacity = JSON_OBJECT_SIZE(3);
DynamicJsonDocument doc(capacity);

int eeAddress = 0; //EEPROM address to start reading from

boolean configBool;

char arr[16];

long int temp_recv = 0; //licznik czasu ktory uplynal od ostatniej wiadomosci

void setup()
{
    // Hardware Serial comunication uart
    Serial.begin(9600);
    // Serial.begin(115200);
    while (!Serial)
        ; // Wait for serial port to be available
    logger.ok(F("setup"), F("Serial for uart comunication succeeded"));
    //---------------------------------------------------------------------------

    // Hardware Serial lora comunication uart
    // Serial2.begin(9600, SERIAL_8N1, RXD2, TXD2);
    Serial2.begin(9600);
    while (!Serial2)
        ;
    logger.ok(F("setup"), F("Serial for lora comunication succeeded"));
    //---------------------------------------------------------------------------

    //  Inicialize pinMode for leds
    pinMode(led1, OUTPUT);
    logger.info(F("setup"), "led1 - error set to pin " + String(led1, DEC));
    pinMode(led2, OUTPUT);
    logger.info(F("setup"), "led2 - setup done set to pin " + String(led2, DEC));
    pinMode(led3, OUTPUT);
    logger.info(F("setup"), "led3 - init success set to pin " + String(led3, DEC));
    pinMode(led4, OUTPUT);
    logger.info(F("setup"), "led4 - flesh write set to pin " + String(led4, DEC));
    //---------------------------------------------------------------------------

    //  Inicialize pinMode for buttons
    pinMode(sw1, INPUT);
    logger.info(F("setup"), "sw1 - right button set to pin " + String(sw1, DEC));
    pinMode(sw2, INPUT);
    logger.info(F("setup"), "sw2 - left button set to pin " + String(sw2, DEC));
    //---------------------------------------------------------------------------

    // Begin EEPROM comunication only for esp
    EEPROM.begin(512);
    logger.ok(F("setup"), F("EEPROM comunication succeeded"));
    //---------------------------------------------------------------------------

    // Lora inicialization
    logger.info(F("setup"), F("Wait for lora to be available"));
    logger.info(F("setup"), F("initing"));
    if (!driver.init())
    {
        logger.error(F("setup"), F("init failed"));
        digitalWrite(led1, HIGH);
        while (1)
            ;
    }
    logger.ok(F("setup"), F("init over"));
    digitalWrite(led3, HIGH);
    //---------------------------------------------------------------------------

    //  Read lora config struct from eeprom
    logger.info(F("setup"), F("Current configuration settings: "));
    readConfig();
    showJSONData();
    resolveConfig();
    //---------------------------------------------------------------------------

    logger.ok(("setup"), F("Setup done"));
    digitalWrite(led2, HIGH);
    //---------------------------------------------------------------------------
}
void loop()
{
    // lora config
    if (digitalRead(sw1) == LOW)
    {
        config();
    }
    // recive lora char
    // else
    // {
    //     if (driver.available()) //czy jest wiadomosc do odebrania?
    //     {

    //         //maksymalna dopuszczalna dlugosc wiadomosci
    //         //wynosi MAX_MESSAGE_LEN = MAX_PAYLOAD_LEN - HEADER_LEN [53 = 58 - 5]
    //         //naglowek dodawany jest automatycznie, oznacza to ze mamy do dyspozycji 55bajtów.
    //         uint8_t buf[RH_E32_MAX_MESSAGE_LEN]; //bufor na wiadomosc
    //         uint8_t len = sizeof(buf);           //ilość znaków

    //         if (driver.recv(buf, &len)) // odebrana wiadomośc zapisujemy w buff
    //         {

    //             //      Serial.print("odebrano wiadomosc : ");
    //             //      Serial.println((char*)buf);
    //             //      Serial.print("o rozmiarze : ");
    //             //      Serial.println(sizeof(buf));
    //             //
    //             //      Serial.print("czas od ostatniej wiadomosci: ");
    //             //      Serial.print(millis() - temp_recv);
    //             //      Serial.println(" [ms]");
    //             //      Serial.println();
    //             Serial.print(F("<"));
    //             Serial.print((char *)buf);
    //             Serial.print(F(","));
    //             Serial.print(millis() - temp_recv);
    //             Serial.print(F(","));
    //             Serial.print(sizeof(buf));
    //             Serial.println(F(">"));

    //             temp_recv = millis();
    //         }
    //         else //jezeli nic nie odebralismy "fail"
    //         {
    //             //                Serial.println(F("recv failed"));
    //             logger.error(F("loop"), F("recv failed"));
    //         }
    //     }
    // }
    // lora recive struct
    else
    {
        if (driver.available()) //czy jest wiadomosc do odebrania?
        {

            struct TRACKER_PACKET incomingData;
            uint8_t len = RH_E32_MAX_MESSAGE_LEN;

            /*Receive message, message stored in buf, len of message stored in len.
              as a result we got info.
              info content:
              Status   <- it's transmission success status,
                MSG_LEN  <- lenght of actual tranmited message + header,
                ID_TX    <- transmiter ID.
                FLAGS    <- user flags.
                MSG_TYPE <-  string or struct.
            */

            PacketInfo info = driver.receiveMessage(&incomingData, &len); //    <----------- recevie message

            Serial.print("Status: ");
            Serial.println(getStatusDescription(info.status));

            if (info.status == L_SUCCESS) // check if Status of transmition is successful.
            {
                print_message(&info, &incomingData);
            }
            else //fail if we receiv nothing - something goes wrong
            {
                Serial.println("recv failed");
            }
        }
    }
}
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

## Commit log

2021-01-14 board
    gps tracker board
    [STM_test_board_1.brd, STM_test_board_1.sch, gps_tracker2.0.brd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]
2021-01-16 receviver
    receiver
    [Power_supply.sch, receiver-BOM.csv, receiver-BOM.xlsx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]
